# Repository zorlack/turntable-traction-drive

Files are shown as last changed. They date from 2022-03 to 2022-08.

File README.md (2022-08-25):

# Turntable Traction Drive Project

<image alt="Design Render" src="images/design-render.jpg" width=600 />

This is my design for a Turntable Traction Drive. It's meant to turn a large theatrical turntable covered in sets and actors in a safe reliable way. It can be built for less than $3000 USD.

I was inspired to take on this project by Alan Hendrickson's chain-driven design featured in [Technical Designs Solutions for Theatre Volume 2 (Sammler/Harvey 2002)](https://www.amazon.com/Technical-Design-Solutions-Theatre-Collection/dp/0240804929). His design shows how a chain drive can rotate a turntable. I was interested in designing an easier-to-integrate "bolt-on" solution.

Feel free to make your own or iterate on this in any way permitted by the [license](LICENSE)! If you do happen to build one, send me a picture, I'd love to share it!

This project [has a website.](https://zorlack.github.io/turntable-traction-drive/)

## Critical Documents

| Document Name | Description |
| -- | -- |
| [Safety and Liability](SAFETY.md) | Discussion of the drive and safety factors associated with its use. |
| [Design Document](DESIGN.md) | Discussion of design and considerations made. |
| [Parts Sourcing Guide](SOURCING.md) | Instructions on how to buy the right parts to build your own Turntable Traction Drive. |
| [Assembly Guide](ASSEMBLY.md) |  Instructions on how to build your own Turntable Traction Drive.  |
| [Integration Guide](INTEGRATION.md) | Instructions for Technical Directors on how to integrate this machine into your set desgin. |
| [Operation Guide](OPERATION.md) | Instructions for Technical Directors on how to operate this machine. |
| [Bill Of Materials](BOM.md) | A list of the parts required to build this machine. |
| [Wiring Guide](WIRING.md) | Instructions for wiring up the VFD, Control Pendant, and Emergency-Stop. |
| [Custom Parts Overview](TurntableTractionDrive-PartsOverview.pdf) | A one-page PDF helpful when ordering custom cut steel. |
| [Creative Commons Attribution 4.0 International](https://github.com/zorlack/turntable-traction-drive/blob/master/LICENSE) | The license under-which these plans are made available. |

## Checklists

| Document Name | Description |
| -- | -- |
| [Integration Checklist](INTEGRATION.md#integration-checklist) | A list of integration requirements for safe scenic integration of the Turntable Traction Drive. |
| [Operations Checklist](OPERATION.md#operations-checklist) | A "preshow" checklist to verify before each use of the Turntable Traction Drive. |

## Part Files

| Part | Description |
| -- | -- |
| [Chassis Parts](https://github.com/zorlack/turntable-traction-drive/tree/master/dxfs) | 2D CAD drawings of chassis parts to be cut from 1/4" mild steel. | 
| [Safety Placard](TurntableTractionDriveLabel.pdf) | A PDF to be made into a printable label and applied to the top of the chassis. | 

## Media

- [Assembled Chassis Before Welding (photo)](parts-fitup.jpg)
  
  <image alt="Assembled Chassis Before Welding (photo)" src="images/parts-fitup.jpg" width=400 />

- [Initial Bench Test (video)](https://youtu.be/k4kjQTp1Dig)
  
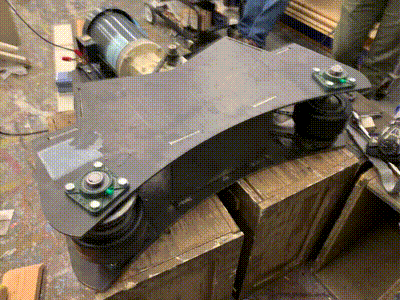
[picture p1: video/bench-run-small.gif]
Bench Test (https://youtu.be/k4kjQTp1Dig)
  

- [Startup Run (video)](https://youtu.be/NJ8Oi7qZh6Y)

  Startup Run (https://youtu.be/NJ8Oi7qZh6Y)

- [Full Speed Run of 23' Turntable (video)](https://youtu.be/Ed3DXH9XDa4)

  Full Speed Run of 23' Turntable (https://youtu.be/Ed3DXH9XDa4)
  
- [Full Speed Run of 6' Turntable (video)](https://youtu.be/193OzLW5t50)

  Full Speed Run of 6' Turntable (video) (https://youtu.be/193OzLW5t50)
  
- [Rehearsing on a 6' Turntable (video)](https://youtu.be/gqXYZ6G5New)

  Rehearsing on a 6' Turntable (video) (https://youtu.be/gqXYZ6G5New)

## Turntable Traction Drive Specifications

| Traction Drive Feature |  Detail |
| --- | ---|
| Design Units | **INCHES** |
| Height | 9.875" |
| Width | 32.875" |
| Depth |  33" |
| Chassis Weight | ~112 Lbs |
| Total Weight | ~228 Lbs |
| Number of Parts | 63 |
| Minimum Turntable Size | 6' Diameter |
| Maximum Turntable Size | Proven on a 23' diameter Turntable with steel and wood scenery. |

### Powerplant Details

My motor decision was based on what I had lying around. You may easily sub in your own motor, but for simplicity of integration try to pick a motor matching NEMA Frame 145TC. Otherwise you may have to drill new holes in the `Base Plate` and `Motor Gusset`.

| Powerplant Feature |  Detail |
| --- | ---|
| Model | General Electric 2HP TEFC (5KE48WN8167) |
| Speed | 1725 RPM at 60Hz |
| Layout | NEMA Frame 145TC |
| Gearhead | Morse 175Q140LR5 |
| Gearhead Ratio | 5:1 |

### Control Details

In order to vary the speed of drive motor we must use a Variable Frequency Drive (VFD). The VFD will be responsible for managing the speed and acceleration of the traction drive. 

#### VFD for 3 Phase Power (208 VAC)
In our environment we have easy and plentiful access to 3phase 208v. For this reason we have selected a 3phase input VFD. If you have access to 3 phase power you can benfit from our integration notes throughout this documentation.

| VFD Feature |  Detail |
| --- | ---|
| Model | Automation Direct DURA Pulse (GS23-22P0)  |
| Input Power | 230V 3-Phase (208 is fine) |
| Output Power | 1.5 KW (2 HP) |
| Output Range | 0 - 600Hz |
| Safe Torque Off (STO) | Yes |

#### VFD for Single Phase (120 VAC)
Our initial testing was performed on a .75 KW 120V VFD. We were able to easily turn the 23' turntable using just a single wall outlet.

| VFD Feature |  Detail |
| --- | ---|
| Model | Hitachi L-100 (L100-007NFU)  |
| Input Power | 120VAC 15A |
| Output Power | 0.75 KW (1 HP) |
| Output Range | 0 - 360Hz |
| Safe Torque Off (STO) | **No** |

We decided to replace this VFD for two reasons:

- In our environment 3-phase 208 is easily availble, and since 1HP isn't really up to the demands of our motor, the testing VFD didn't make a lot of sense.
- The intial wiring design of our e-stop buttons was not up to industrial automation standards. Critically, the e-stop was unable to constrain a runaway VFD. As a hedge agasint this risk we have selected a VFD with a Safe Torque Off (STO) feature. This feature adds independant hardware designed to reliably disconnect the output transistors of the VFD from the motor.

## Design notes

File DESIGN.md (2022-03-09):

# Turntable Traction Drive Design

Staples Players was looking for a way to add some automation and motion to its production of Disney's Descendants The Musical. I was interested in creating a solution which could be applied generically to any of the typical turntable configurations they use.

I decided to make a drive unit to rotate a turntable by applying a traction wheel against the edge of the table. Such a device would be easy to integrate in most sets where the turntable sits on top of the stage floor.

## Mechanical Considerations

Using drive wheels to turn a turntable seemed pretty straight forward. I'm pretty sure I've seen carnival rides driven in this manner. As a gut-check I did a bit of marketplace research and found that such devices do exist.

<image alt="Concept" src="images/initial-concept.png" width=600 />

My first idea was to use a motor with a gear reduction and a triangular chain configuration. The friction wheels would be pneumatic tires. The idea was that an idler would pull the chain away from the contact-point of the turntable and allow for easy tensioning of the chain system. However, preliminary research indicated two things: First, chains don't like to be run horizontally they prefer to run vertically. Second, a triangular configuation would result in an uneven distribution of power between the two drive wheels.

<image alt="Design Layout" src="images/design-layout.jpg" width=400 />

Moving away from the single-chain configuration I moved towards a centrally mounted motor with two chains, one going to each drive shaft. I also ditched the idea of pneumatic wheels and prefering instead an off-the-shelf keyed drive roller from McMaster. This simplified sourcing and answered the question: How do I attach the drive shaft to the wheel.

<image alt="Design Render" src="images/design-render.jpg" width=400 />

With those two decisions made the next step was to make a design in Fusion 360 and start selecting components. I started with the power source. I was eager to use a motor I had sitting on the shelf: A 3 Phase 2HP GE Motor (NEMA Frame 145TC. GE Model 5KE48WN8167) with a Morse 5:1 right-angle gear reduction (Morse 175Q140LR5.) This is a fairly beefy motor with a significant gear reduction.

| |  Motor Shaft | Gear Box Output | Output Wheel |
| -- | --- | -- | -- |
| Ratio | 1:1 (1.0) | 5:1 (.20) | 11:30 (.36) |
| RPM @ 60Hz | 1725 RPM | 345 RPM | 124 RPM |

In addition to the gear reduction on the front-end of the motor, I wanted to further reduce the gearing for two reasons: First, turntables typically require a large amount of effort to break free when turning. Reduced gearing would permit greater starting torque. Second, the native speed of the motor and gearing is 345 RPM (1725 RPM / 5). We want the traction drive gearing to allow us to use as much of the 0-60Hz range of the motor as possible without spinning a turntable too quickly. Therefore care was taken to use a small drive sprocket (11 teeth), a large axle-sprocket (30 teeth), and a small drive wheel (6" diameter".)

| Effective Speed Math | |  |
| -- | -- | -- |
| Drive Wheel Circumference (feet) | 2π * .25' | 1.57' Foot Circumference |
| Linear Feet Per Minute | 124 RPM * 1.57' | 194 Feet Per Minute |
| 6' Diameter Turntable Max Speed | 194 FPM ÷ 19' | 10.2 RPM (Measured: 11.3 RPM) |
| 16' Diameter Turntable Max Speed | 194 FPM ÷ 50' | 3.8 RPM |
| 23' Diameter Turntable Max Speed | 194 FPM ÷ 72' | 2.6 RPM (Measured: 2.7 RPM)|

**Integration Note:** *If you find that the drive speed is not large enough for your large turntable design, your best bet, depending on your choise of motor and VFD, is to overdrive the motor past 60Hz. (Most VFDs let you run up to 360Hz, but you will want to check your motor and drive documentation first.) Alternatively you could swap out the 6" drive wheels for a larger diameter wheel, but be aware that this will reduce the available startup torque.*

<image alt="Right Bearing Gusset" src="images/right-gusset.jpg" width=400 />

The Turntable Traction Drive is designed to sit on a flat surface. Because of this I couldn't through-bolt the pillow block bearings. That means that the steel would have to be drilled and tapped. Because the steel is only 1/4" I would need additional thickness on the bottom layer in order to have appropriate thread engagement. To resolve this, I designed three "gusset" parts: Two supporting the lower bearings and one supporting the motor mount. They are meant to be welded down then drilled and tapped, such that the threads are continuous.

## Turntable Eccentricity

Turntables aren't perfect circles, and they're not always perfectly centered, so I needed somehow to keep the machine pressed against the side of the turntable even if it's out-of-true. I designed the machine with four 200lb springs which could be set to provide significant preload against the side of the turntable. 

<image alt="Pusher Springs" src="images/pusher-plate.jpg" width=400 />

The springs are held captive by a 5/16" bolt welded to the pusher plate. The springs press against a piece of 1.5" angle iron which is lag-bolted through the two slots to the stage floor. This allows the whole machine to slide back and forth in response to bulges or dips in the circumference of the turntable.

<image alt="Ratchet Straps" src="images/ratchet-straps.jpg" width=400 />

When testing we found that a far simpler solution was to use ratchet straps to draw the machine up against the side of the turntable and hold it there. Ratchet straps have some natural elasticity and therefore provide similar preload to a spring-based solution with substantially easier integration. (We can turn a large turntable witout even bolting the machine to the deck!)

## Chain Tension

Chain based system must be kept in tension to keep the chain from slipping off the drive sprocket. In order to apply tension to the system we mounted the drive motor on top of [an adjustable sled from McMaster](https://www.mcmaster.com/62035K23/). However, we noticed too late that the sled is meant to adjust the position of a motor mounted perpendicularly to the track of the sled. My design called for the motor to be mounted parallel with the track.

<image alt="Motor Modifications" src="images/motor-mods.jpg" width=200 />

In order to mount the motor in this orientation we had to drill two additional holes in the motor's NEMA 146TC mounting plate. Once drilled we could use the drive seld to tension the chain and then crank down the motor bolts to lock it in place.

## Material

Because I didn't know how much force would be required to turn a loaded-turntable I wasn't able to do any real load calculations. Without this knowlege it seemed the best bet was to over-build the system. So I designed around plasma-cut 1/4" A36 mild steel. 

<a href="TurntableTractionDrive-PartsOverview.pdf"><image alt="Steel Order" src="images/design-sample.jpg" width=400 /></a>

I made a tab-and-slot design such that when assembled the machine would (hopefully) hold itself square long enough for me to weld it together. I allowed for 1/16th of clearance between my tabs and my slots and verified that the steel shop could hold 1/16 tolerance during plasma cutting. Their advice was that as long as no holes were smaller than 0.25" they should have no problems holding 1/16" tol.

<image alt="Steel Order" src="images/steel-qa.jpg" width=400 />

I provided the steel shop with a flat DXF file for each part with **INCHES** as the unit. They sent me back some fully dimensioned scans for me to verify.

<image alt="Parts Fitup" src="images/parts-fitup.jpg" width=400 />

Chapin and Bangs in Bridgeport, CT made the steel parts. They were made out of A36 steel, plasma cut, delivered dry. The cost was $810 with delivery.

<image alt="Initial Welds" src="images/initial-welds.jpg" width=400 />

The biggest problem with 1/4" steel is that my welder is only barely powerful enough to weld it. I ended up using .030 flux-core wire. Flux-core welds don't look great but they're plenty strong and I was able to get reasonable penetration even with my wimpy 120VAC welder.

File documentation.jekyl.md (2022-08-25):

---
permalink: /documentation
title: Turntable Traction Drive
description: Complete Documentation
---

<image alt="Design Render" src="images/design-render.jpg" width=600 />

This is my design for a Turntable Traction Drive. It's meant to turn a large theatrical turntable covered in sets and actors in a safe reliable way. It can be built for less than $3000 USD.

I was inspired to take on this project by Alan Hendrickson's chain-driven design featured in [Technical Designs Solutions for Theatre Volume 2 (Sammler/Harvey 2002)](https://www.amazon.com/Technical-Design-Solutions-Theatre-Collection/dp/0240804929). His design shows how a chain drive can rotate a turntable. I was interested in designing an easier-to-integrate "bolt-on" solution.

# Table of Contents

- [Safety](#safety-and-liability)
- [Design Document](#turntable-traction-drive-design)
- [Parts Sourcing Guide](#parts-sourcing-guide)
- [Assembly Guide](#turntable-traction-drive-assembly-guide)
- [Integration Guide](#turntable-traction-drive-integration-guide)
- [Operation Guide](#turntable-traction-drive-operation-guide)
- [Bill of Materials](#bill-of-materials)
- [Wiring Guide](#wiring-guide)
- [License](#license)

{% include_relative  SAFETY.md %}

{% include_relative  DESIGN.md %}

{% include_relative  SOURCING.md %}

{% include_relative  ASSEMBLY.md %}

{% include_relative  INTEGRATION.md %}

{% include_relative  OPERATION.md %}

{% include_relative  BOM.md %}

{% include_relative  WIRING.md %}

# License
```
{% include_relative LICENSE %}
```

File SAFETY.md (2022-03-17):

# Turntable Traction Drive Safety and Liability

As it's intended use involves live actors on a rotating stage, the safety of the Turntable Traction Drive must be considered seriously. But before we dig into a risk assesment understand this: 

**I am not an engineer.** I write software for a living and am not formally trained to assess safety risks. As such, **any risk assesment made here should not be considered comprehensive.**

In undertaking this project, and making it publicly available, it behooves me to draw attention to this fact, as well as to to state clearly that **I don't guarantee that this design works as intended, and I am not liable for any harm resulting from your use of this design.**

## Liability

This design is available for use under the [Creative Commons Attribution 4.0 International license](https://github.com/zorlack/turntable-traction-drive/blob/master/LICENSE). By using this design you agree to the terms of this license.

The license includes the following language, which you should read:

    Section 5 -- Disclaimer of Warranties and Limitation of Liability.

      a. UNLESS OTHERWISE SEPARATELY UNDERTAKEN BY THE LICENSOR, TO THE
         EXTENT POSSIBLE, THE LICENSOR OFFERS THE LICENSED MATERIAL AS-IS
         AND AS-AVAILABLE, AND MAKES NO REPRESENTATIONS OR WARRANTIES OF
         ANY KIND CONCERNING THE LICENSED MATERIAL, WHETHER EXPRESS,
         IMPLIED, STATUTORY, OR OTHER. THIS INCLUDES, WITHOUT LIMITATION,
         WARRANTIES OF TITLE, MERCHANTABILITY, FITNESS FOR A PARTICULAR
         PURPOSE, NON-INFRINGEMENT, ABSENCE OF LATENT OR OTHER DEFECTS,
         ACCURACY, OR THE PRESENCE OR ABSENCE OF ERRORS, WHETHER OR NOT
         KNOWN OR DISCOVERABLE. WHERE DISCLAIMERS OF WARRANTIES ARE NOT
         ALLOWED IN FULL OR IN PART, THIS DISCLAIMER MAY NOT APPLY TO YOU.

      b. TO THE EXTENT POSSIBLE, IN NO EVENT WILL THE LICENSOR BE LIABLE
         TO YOU ON ANY LEGAL THEORY (INCLUDING, WITHOUT LIMITATION,
         NEGLIGENCE) OR OTHERWISE FOR ANY DIRECT, SPECIAL, INDIRECT,
         INCIDENTAL, CONSEQUENTIAL, PUNITIVE, EXEMPLARY, OR OTHER LOSSES,
         COSTS, EXPENSES, OR DAMAGES ARISING OUT OF THIS PUBLIC LICENSE OR
         USE OF THE LICENSED MATERIAL, EVEN IF THE LICENSOR HAS BEEN
         ADVISED OF THE POSSIBILITY OF SUCH LOSSES, COSTS, EXPENSES, OR
         DAMAGES. WHERE A LIMITATION OF LIABILITY IS NOT ALLOWED IN FULL OR
         IN PART, THIS LIMITATION MAY NOT APPLY TO YOU.

In plain language: **I don't guarantee that this design works as intended, and I am not liable for any harm resulting from your use of this design.**

## Limitations

The Turntable Traction Drive has the following known limitations/deficiencies:

- No Brake: The Turntable Traction Drive does not provide built-in braking. (This may be remedied by using a motor configuration with a power-off brake.) In practice this means that when the drive is not rotating the turntable is only kept in place by two things: The inertia of the turntable itself, and the friction in the chain and gearbox system of the Turntable Traction Drive. For massive (high-mass) turntables with substantial loss due to friction this is not a problem, as the turntable will tend to stay put. **For low-mass or low-friction turntables it may be neccessary to use an external braking mechanism to keep the turntable from free-rotation when the drive is not rotating.**
- Insufficient Current Limiting Capabilities: Ideally we would like to set a current limit at various stages of operation such that the inverter trips when there is an unexpected spike in current. **The Hitachi L100-007NFU does not have sufficiently granular current-limit controls.**
- Open Loop: The Turntable Traction Drive is a machine for rotating a turntable. It is not a machine for accurately "positioning" a turntable. As such **this machine's utility in precise motion control applications may be limited.**

## Key Safety Principals

:warning: **The Turntable Traction Drive is a powerful machine. Using it should not be taken lightly. Caution and care must be taken in every integration to ensure that safe operating parameters are configured.**

A turntable may pose a hazard on set even when operated manually by backstage technicians, however, unlike backstage technicians this machine has no brain. It doesn't know to stop because a piece of scenery is late during a scene-shift. It is not context-aware. Also, unlike a backstage technician, under the right circumstances this machine can summon inhuman amounts of torque.

:warning: **Due to its power and remoteness this machine is not designed as part of an automation system. Rather, it is intended to be manually operated by a user with a clear view of the turntable.**

The Turntable Traction Drive has exposed moving parts and therefore poses some first-hand risk of injury to operators. However, when attached to a turntable new hazards may appear.

:warning: **A scenic turntable creates risks of injury independant of the drive mechanism. Take care to evaluate the risks not just from the Turntable Traction Drive, but from the system as a whole.**

## Risk Management

As some risk is unavoidable, my analysis will focus on mitigation strategies. Any requirement layed out in this section must be specifically required in either the Integration Checklist or Operations Checklist.

| Risk | Mitigation Strategy |
| -- | -- |
| Risk of electrical shock | **Requirements:**<br/>Ground VFD appropriately to input mains.<br/>Ground motor appropriately to VFD.<br/>Ground chassis appropriately to the motor chassis. |
| Pinching hazards from exposed rotating machine parts. |  **Requirement:**<br/>Turntable Traction Drive must be in a fully enclosed secure area during operation. |
| Pinching/Crushing hazards between traction wheels and turntable edge. | **Requirement:**<br/>Interface between the turntable and the traction drive must be fully enclosed during operation. |
| Risk of unexpected start | **Requirement:**<br/>Enable Unattended Start Protection in VFD by setting `c04` to `13` and short `P24` to `PIN 4`<br/>Disconnect power from the system prior to maintenance. |
| Risk of fall during normal operation | **Requirements:**<br/>Rehearse with onstage personel in order to find safe speeds and acceleration values. Do not deviate from these values without notice. |
| Risk of fall due to sudden acceleration | **Requirement:**<br/>Use conservative acceleration/deceleration values when configuring VFD. (For Hitachi L-100 see settings `f01`, `f02`, and `f03`) |
| Risk of fall due to overspeed | **Requirement:**<br/>Set a conservative hard frequency limit in your VFD configuration. (For Hitachi L-100 see settting `a61`) |
| Risk of crushing | **Requirement**<br/>Where possible tune-narrowly the current limiting features of your VFD. (For the Hitachi L-100 this configuration may be limited.) |
| Risk of crushing because of external scenery-based crush points. | **Requirements:**<br/>Turntables must maintain a raidal safety margin sufficient to prevent a person from being caught between a rotating piece of scenery and any adjacent piece of scenery.<br/>Emergency Stop button must located near the turntable.<br/>Cast and crew must be trained on the location of the Emergency Stop button. |
| Risk of entanglement | **Requirements:**<br/>Operator must have a clear view of the turntable.<br/>Emergency Stop button must located near the turntable.<br/>Cast and crew must be trained on the location of the Emergency Stop button. |
| Risk of slipping on a free-rotating turntable | **Requirement**<br/>A parking brake (or other disablement device) must be employed to prevent the turntable from turning when the Turntable Traction Drive is not in use.<br/>All on-stage personel must be instructed on the free-rotating-nature of the turntable. |
| Risk of operator/integrator ignorance | **Requirements:**<br/>All safety requirements and warnings must be clearly printed on a label applied to the machine.<br/>Documentation must be made available. |
| Risk of structural collapse on turntable | **Requirement:**<br/>Ensure that all scenery is constructed such that it can absorb tortional load such as might result from a sudden change in rotational speed. |

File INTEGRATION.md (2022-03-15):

# Turntable Traction Drive Integration Guide

This guide is designed to help scenic designers and technical directors integrate the Turntable Traction Drive into their sets.

:warning: **Before Proceeding, make sure you have read and understood the [SAFETY](SAFETY.md) section of the documentation.**

:warning: **Before Proceeding, make sure you have read and understood the [Limitations](SAFETY.md#Limitations) section of the documentation.**

## Turntable Integration

The Turntable Traction Drive applies significant forces to the side of the turntable where it makes contact. This requires the following considerations:

- The Turntable Traction Drive should not be pressed against a surface which will bow or deflect under pressure. Ideally you'd want a 3" wide rigid band that the turntable can drive against. In practice we've found that the drive wheels can get plenty of traction when applied against the edge of a 1.5" laminated plywood floor.
- The drive wheels of the traction drive may cause maring or discoloration of surface finishes. You may need to apply a protective coating to traction surfaces if they are visible to the audience.
- The drive wheels of the traction drive apply force to just one side of a turntable. To keep the turntable centered on its rollers your centering device must be sufficiently rigid (and well lubricated) to counter this force. 

### Critical Dimensions

The two key factors when determining if this machine will work with your turntable are diameter and mass. At present we don't have sufficient information to give guidance about maximum turntable mass. Except to say that we had no difficulty moving a 23' turntable with a 2-story wood and steel "castle" on it.

| Dimension | Value |
| -- | -- |
| Minimum Turntable Diameter | 6' |
| Maximum Turntable Diameter | 23' Demonstrated (Maximum Unknown) |

If the diameter of your turntable is too large you may have difficulty running it fast enough with the as-designed gearing. If this is the case you have two options:

- You may increase the diameter of your drive rollers up to 12" in diameter (this size is quite extreme consider 8"). Increasing the diameter of the drive rollers will cause you to suffer a substantial loss of starting torque. The advantage is increased speed at your motor's native frequency without an increase in chain noise. 
- You may decide to overdrive your motor beyond 60Hz. Many VFDs will let you run the motor up to 400Hz, at this speed you would likely damage your gearbox, motor and chain drive. Many motors will be perfectly happy to run faster than 60Hz with reduced duty cycle. Consult your motor and gearbox documentation to determine the maximum safe operating speed of your Turntable Traction Drive.

Another critical factor is the height of the traction-bearing surface relative the bottom of the turntable traction drive. The vertical position of the drive wheels is adjustable, but is ultimately constrined by the spacing between the drive sprockets. That said drive wheels have about 4" of vertical adjustability.

| Dimension | Value |
| -- | -- |
| Minimum Traction Surface Width | 1.5" |
| Maximum Traction Surface Width | 3" (Drive Roller Width) |
| Lowest Possible Traction Surface | 3.25" to 4.75" from the bottom of the machine |
| Highest Possible Traction Surface | 5.75" to 7.25" from the bottom of the machine |

If the traction surface of your turntable is too high, it may be neccesary to raise the machine so that it contacts the correct portion of the turntable. Conversely, it may be neccesary to mount your traction drive below the stage if your dive surface is too low.

## Traction Pressure

The available tractive force of the Turntable Traction Drive is related to the pressure applied by the rollers against the traction surface. In other words, it's not sufficient to place the Turntable Traction Drive next to a turntable, it must be pressed firmly against the side of it. 

This "preload" pressure may be created via two integration schemes:

### Ratchet Straps

In testing the Turntable Traction Drive we observed that we could apply ample force between the drive wheels and the turntable simply by connecting ratchet straps between the machine chassis and the carrier wheels of the turntable.

This system has several advantages over the Pusher Spring system:

- Rachet straps are plentiful and easy to inspect.
- The have some natural stretch to them, allowing for eccentricity of the turntable.
- They are easy to remove and reattach, simplifying maintenance activities.
- Rachet straps don't create metal-on-metal noise as they stretch.

For these reasons ratchet straps are prefered mecahnism for integration.

To attach the turntable via rachet straps:

- Ensure that the Turntable Traction Drive is evenly supported and that you have strong material under the lag-bolt slots.
- Connect the left and right sides between the rear of the side-panels and a suitably strong tie-down point on or near your turntable.
- Evenly tension the two belts such that drive wheels are in good contact with the turntable.
- Lag-bolt the machine down to the supporting surface loosely. (Such that the machine may become detached from the turntable, but may not be flung away from it.)

### Pusher Springs

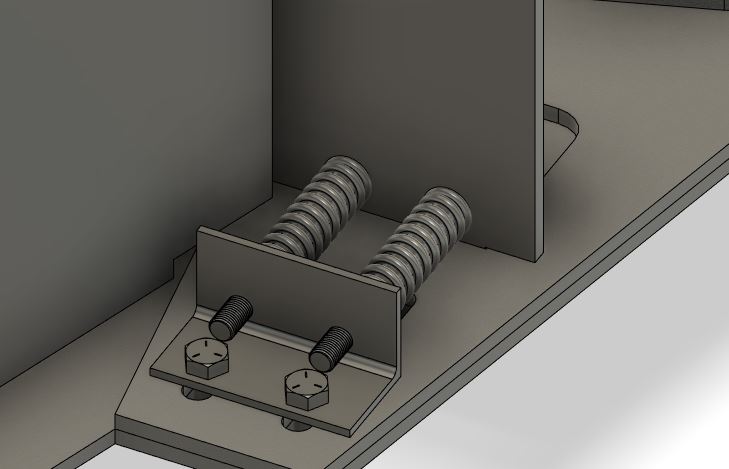
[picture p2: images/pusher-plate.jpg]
Pusher Springs


The design calls for the use of four pusher springs which ride on 5/16" guide bolts. These pusher springs push the turntable forward, away from two L-iron brackets anchored firmly to the deck. This mechanism allows for approximately 1.8" of eccentricity in the turntable circumference while applying around 200 lbs of force.

To install the pusher springs follow these instructions:

- Ensure that the Turntable Traction Drive is evenly supported and that you have strong material under the lag-bolt slots.
- Weld hex-heads the 5/16" partially-threaded guide bolts into the four holes provided in the pusher plates. The bolts should face backwards with the bolt heads resting on the interior faces of the pusher plates.
- Slide the pusher springs over the guide bolts.
- Pass the guide bolts into holes drilled in the L-iron. 
- Using 5/16" lock nuts, compress the pusher springs between the L-Iron and the pusher plates.
- Using lag-bolts, bolt the L-iron to the supporting surface. Make sure the lag-bolts pass through the slots on the bottom plate.
- Loosen the 5/16" lock nuts such that the springs expand between staticaly mounted L-iron and the movable Turntable Traction Drive.

*Note: In the pusher spring rendering there is insufficent clearance between the guide-bolts and the lag-bolts. This has been remedied by raising the holes in the pusher plate.*

## Integration Checklist

To help ensure safe operation of this Turntable Traction Drive please ensure the following **REQUIRED** conditions have been met:

| Requirement | Complete |
| -- | -- |
| Technical Director/Integrator must read and understand the [safety](SAFETY.md) section of this documentation. | :black_square_button: |
| Turntable Traction Drive chassis grounded to motor frame | :black_square_button: |
| Motor frame grounded to VFD | :black_square_button: |
| Turntable Traction Drive is fully enclosed in a secure area | :black_square_button: |
| Drive-wheel interface points are fully enclosed | :black_square_button: |
| Turntable hard-scenery elements don't create opportunities for shearing or crushing | :black_square_button: |
| Emergency stop button located within 6' of Turntable Traction Drive | :black_square_button: |
| Turntable fitted with an external parking brake (or other disablement device.) | :black_square_button: |

## VFD Configuration

### DURApulse GS23-22P0 Configuration

**Note:** These notes are only really useful for the DURApulse GS23. If you're using another VFD consult your documentation.

When configured correctly we desire the following outcome:

- To tell the turntable to run forward short `DCM` to `DI1/FWD`.
- To tell the turntable to run in revers short `DCM` to `DI2/REV`.
- To enter Safe Torque Off `STO` interrupt short between `+24 V` and either `STO1` or `STO2`

#### DURApulse GS23 Parameters

| Parameter | Value | Notes |
| -- | -- | -- |
| `P02.00` | `2` | 2-Wire Configuration |
| `P01.10` | `60` | Output Frequency Upper Limit |
| `P01.12` | `1` | Acceleration Time 1 |
| `P01.13` | `1` | Deceleration Time 1 |
| `P06.12` | ?? | Current Limit 0-250% |

### Hitachi L100 Configuration

**Note:** These notes are only really useful for the Hitachi L-100. If you're using another VFD consult your documentation.

`P24` provides a 24V field reference voltage for use when powering the Control Terminals.

When configured correctly we desire the following outcome:

- To tell the turntable to run forward short `P24` to `PIN 1`.
- To tell the turntable to run in revers short `P24` to `PIN 2`.

#### Hitachi L100 Parameters

| Parameter | Value | Notes |
| -- | -- | -- |
| `a01` | `00` | `00`=Keypad/Potentiometer, `01`=Control Terminals, `02`=F01 Settings |
| `a02` | `02` | `01`=Control Terminals, `02`=Keypad Run Key |
| `a02` | `02` | `01`=Control Terminals, `02`=Keypad Run Key |
| `a61` | `60` | Set a hard limit on the output frequency of the VFD to never overdrive the motor. |
| `a04` | `60` | Set the "Base" Frequency. (The frequency at which the VFD emits full voltage) |
| `a05` | `60` | Set the "Max" Frequency (The frequency allowed during manual opeation) |
| `a97` | `00` | Set the Acceleration Curve: `00`=Linear, `01`=S-Curve |
| `a97` | `00` | Set the Deceleration Curve: `00`=Linear, `01`=S-Curve |
| `c01` | `00` | Configure Terminal 1: `00`=Run Forward
| `c02` | `01` | Configure Terminal 2: `01`=Run Reverse
| `f01` | `nn` | **Set the target frequency** |
| `f02` | `nn` | **Set the acceleration time** (The number of seconds it should take to get spin-up from 0Hz to `f01`Hz) |
| `f03` | `nn` | **Set the deceleration time** (The number of seconds it should take to get spin-down from `f01`Hz to 0Hz) |

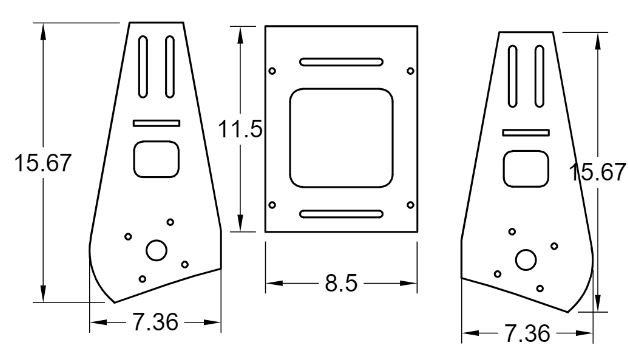
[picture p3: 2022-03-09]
images/design-sample.jpg

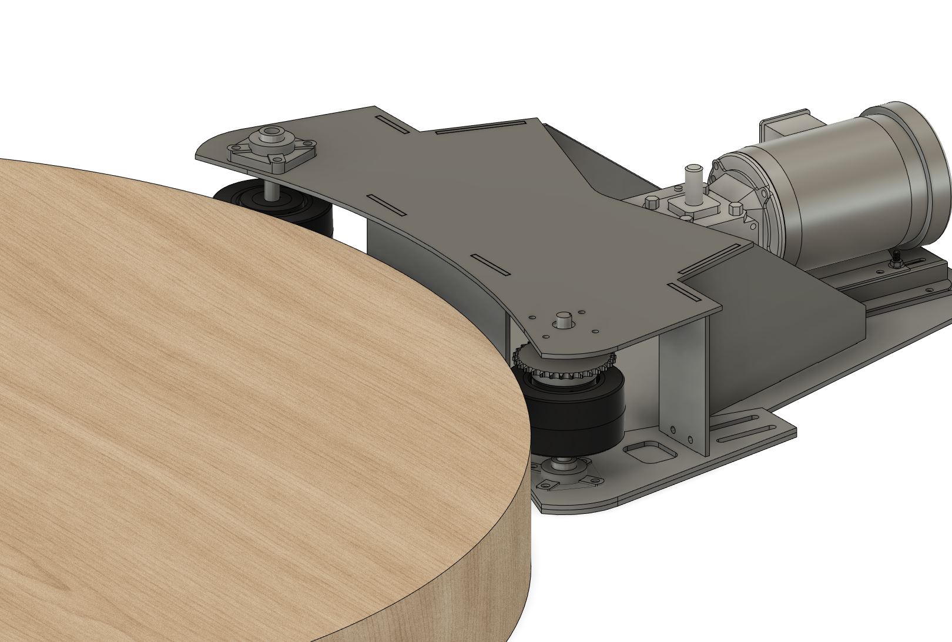
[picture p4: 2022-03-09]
images/design-render.jpg

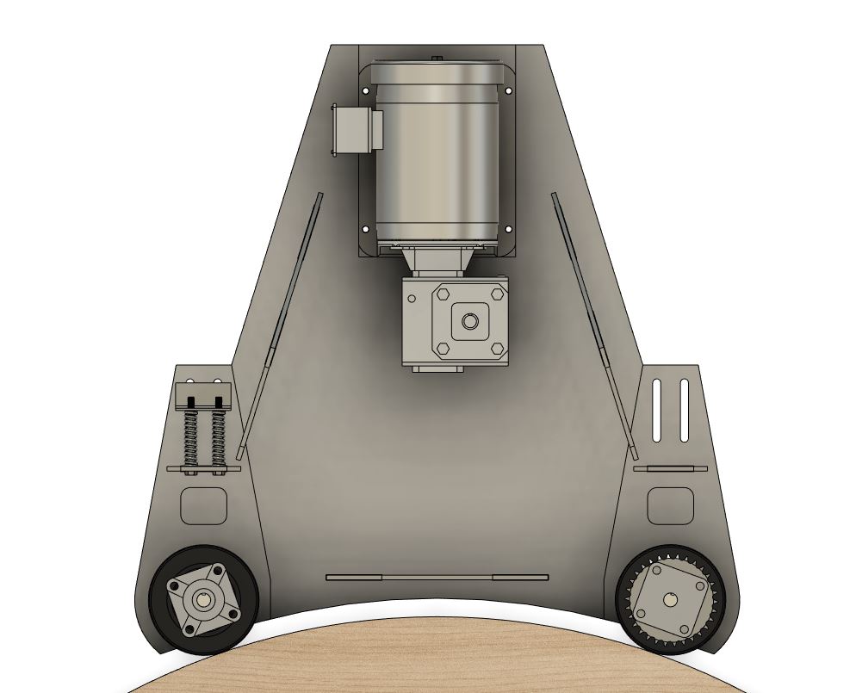
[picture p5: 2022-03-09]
images/design-layout.jpg

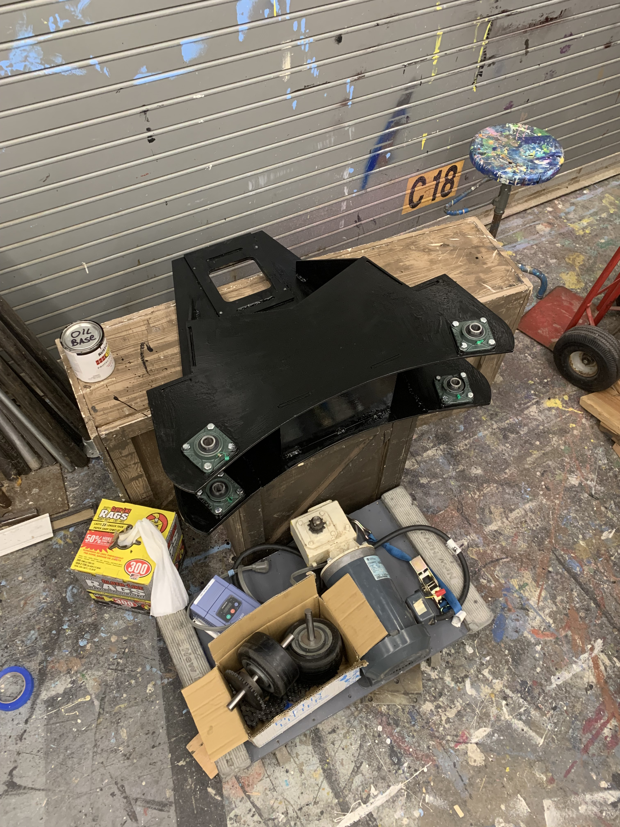
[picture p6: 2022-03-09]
images/painted-chassis.jpg

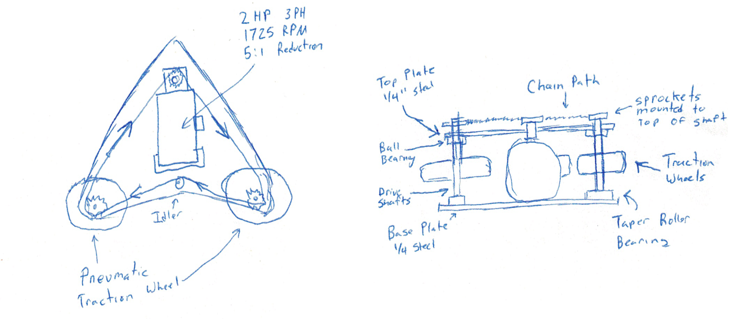
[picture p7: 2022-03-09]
images/initial-concept.png

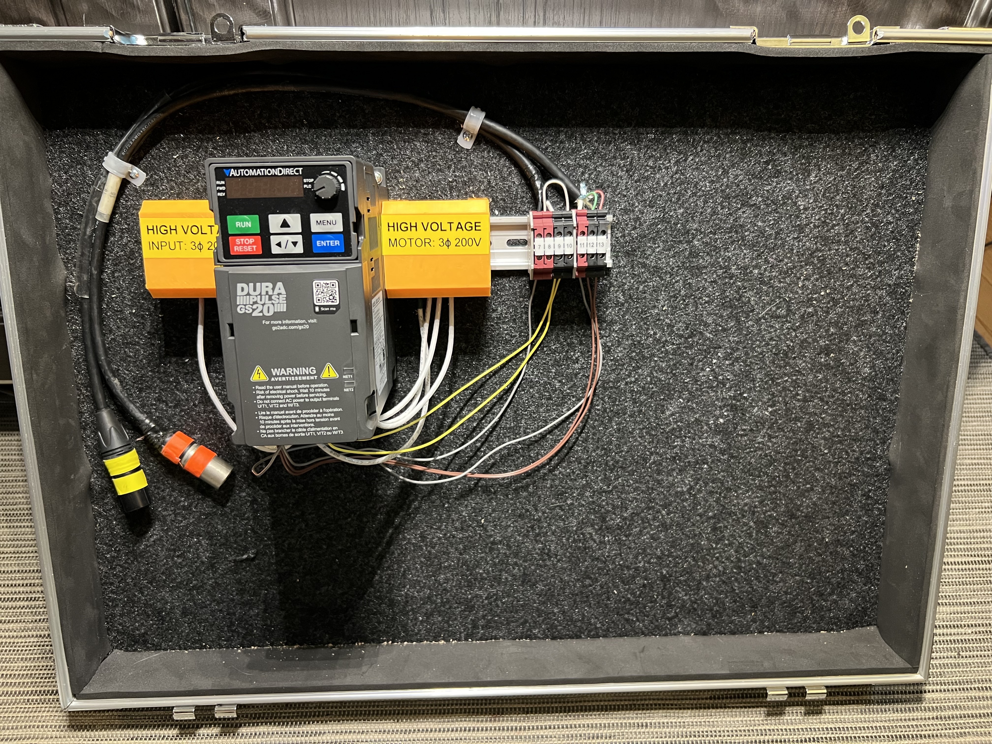
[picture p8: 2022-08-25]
images/control-panel.jpg

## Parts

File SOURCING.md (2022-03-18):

# Parts Sourcing Guide

Finding reliable sources for parts is a challenging problem. If you pick a vendor like Amazon you may find that your item SKUs are no longer available weeks after you've made a purchase. On the other hand if you source parts exclusively from McMaster-Carr and Grainger you'll be paying top-dollar for that consistency.

In order to make parts-sourcing consistant I've chosen McMaster-Carr for most pieces of hardware. The Motor, Gearbox, VFD and Custom Steel you will need to source independently.

## Bill Of Material

This project has a [Bill of Material](BOM.md). The BOM is a list of all the parts we used construct this machine. Wherever possible I have added links which (hopefully) will not go stale quickly. In addition I've added price estimates, but you should expect these numbers to change with time.

I reccomend that you source the hard parts first before placing a large order with McMaster-Carr. Make sure you can find all the relevant components at a price-point which meets your budget before you click "Check Out."

## Sourcing The Motor

The motor, and gearbox can be the most difficult parts to source. If you try to match precisely what I have used you will end up paying top-dollar. A more economical way to source the powertrain is to go on ebay and look for a used parts. Here are the important parameters:

| Feature | Value |
| -- | -- |
| NEMA Frame | 145TC |
| RPM | 1725 |
| Voltage | 208-230 |
| Phases | 3 |

The frame designation describes the precise size and layout of the motor bolts and face. Motor RPM is listed because a 1725 (or 1800RPM) motor is better suited for high-torque applications. Voltage isn't really your problem (since the VFD will be creating the motor voltage) all you really want to do is make sure you're selected a 200V class motor. Three phase is specified because this is necesary for the inverter to control the speed of the motor.

If you deviate too much from this prescription you may have to customize the `Base Plate` and `Motor Gusset` parts in order to fit your motor. You will also have to make sure your gear-reduction fits correctly.

## Sourcing The Gearbox

The gearbox we're using, a Morse 175Q140LR5, has a couple of important features:

| Feature | Value |
| -- | -- |
| Drive Ratio | 5:1 |
| Frame | 143/145TC |
| Shaft Output | Left + Right |
| Output Shaft Diameter | 7/8" |

This may be the hardest part to source cheaply. Ebay may be your best bet. You can be a bit flexible regarding the drive ratio and the output shaft diameter (if you vary the output shaft diameter you will have to choosed different sprockets from the BOM.)

## Sourcing The Variable Frequency Drive (VFD)

The Variable Frequency Drive (also commonly called an inverter) is an esential component of this system. It provides speed control and safety features neceesary to safely operate the Turntable Traction Drive.

For our implementation we have selected AutomationDirect's DURApulse GS23-22P0 VFD. We used the following selection criteria:

| Feature | Value | Note | Required |
| -- | -- | -- | -- |
| Number of Input Phases | 3&nbsp;(or&nbsp;1) | **This matches the supply we have access to.**<br/>We have easy-access to three-phase power, so this is a good choice for our environment. | YES |
| Nominal Input Voltage | 230&nbsp;VAC | **This matches the supply we have access to.**<br/>We have 3-phase 208VAC so this is the correct model. | YES |
| Horsepower By Phase | 2&nbsp;(or&nbsp;1) | **This matches the motor we have selected.**<br/>We have selected a 2HP motor, so we want a VFD rated for 2HP. The parentheses indicates that this VFD can power a 1HP motor when configured for single-phase 200VAC service. | YES |
| Safe Torque Off (STO) | YES | **This is safety requirement used by our e-stop system.**<br/>Having an STO feature means that our e-stop wiring will protect us even from a malfunction of the VFD itself. | YES |
| Current Limit Capability | 10%-250% | **This is a safety requirement.**<br/>This feature allows us to tune the max current available to the motor. This can help stall the system if there's an unexpected jam. | YES |
| UL/CE Listed | YES | Someone has looked at this device to make sure it meets minimum requirements for electrical safety. | NO |
| Freely available software. | YES | Having good software makes integration easier and can improve safety. | NO |
| Software Interface | USB | For PC-based configuration, USB is slightly easier to interface with than RS485. Even USB-B. | NO |
| Cost | $208 | That's a great price for the feature-set we're looking for. | NO |
| SEO | Excellent | Let's be honest, the reason I zeroed in on this VFD is that Automation Direct has good online advertising and search engine optimization. | NO |

### 120VAC Power Single Phase

We have successfully powered our traction drive using a single 20A 120VAC mains circuit connected to a Hitachi L-100 VFD. If you only have access to single-phase 120VAC power you should seek a VFD which matches this configuration. Be aware that you will never be able to run a 2HP motor at maximum power using a 1HP VFD. You will likely also want to reduce your duty cycle in this configuration and should expect to produce extra heat. **That said, we had no difficulty in rotating our 23' turntable on a single 120VAC 20A circuit.**

Also be aware that VFDs under load have a nasty habbit of tripping residential breakers (especially RCD/GFCI circuits.)

## Sourcing the Custom Steel Parts

I found that it was a relatively simple matter to provide a local steel shop with the [2D DXFs](dxfs/) and the [Custom Parts Overview](TurntableTractionDrive-PartsOverview.pdf). The PDF makes it easy for a sales guy to quote the job without needing CAD. The PDF also communicates expectations around minimum hole diameter and tolerances.

The design allows for 1/16 of slop between slots and tabs. The steel fabiractor must be able to hold 1/16th tolerance. The steel company which we worked with said that their plasma process could hold 1/16" of tollerance, but they had a specific requirement that no holes be smaller than 1/4" in diameter. This is not a problem for this design as we have so indicated in the [Custom Parts Overview](TurntableTractionDrive-PartsOverview.pdf).

The total weight of the custom parts is around 112 lbs. Make sure you have a spot where the steel shop can deliver the order easily. In our experience the parts are, individually, easy to move around. When bundled together as a single order the steel is a two-person lift.

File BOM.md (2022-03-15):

## Bill Of Materials

| Component | Units | Quantity | Unit Cost | Notes |
| -- | -- | -- | -- | -- |
| **Control** | | | | |
| Automation Direct DURApulse GS23-22P0* | EA | 1 | $208 | [Variable Frequency Drive](https://www.automationdirect.com/adc/shopping/catalog/drives_-a-_soft_starters/ac_variable_frequency_drives_(vfd)/general_purpose/gs23-22p0) |
| Automation Direct GS20A-DR-AB | EA | 1 | $5 | [VFD 35mm DIN rail adapter.](https://www.automationdirect.com/adc/shopping/catalog/drives_-a-_soft_starters/ac_variable_frequency_drives_(vfd)/remote_keypads,_disconnects,_mounting_-a-_accessories/gs20a-dr-ab) |
| VFD Power Cable | EA | 1 | | #10 3-Wire Appliance Cable |
| VFD Power Connector | EA | 1 | | NEMA 5-15P |
| Control Pendant | EA | 1 | $36 | [Compact Crane Control Pendant](https://www.amazon.com/dp/B077NG3SLZ) |
| Emergency Stop Buttons | PACK | 1 | $14 | Mushroom Cap E-Stop Buttons |
| **Chassis** | | | | |
| Bottom Plate | EA | 1 | -- | Custom 1/4" Steel from [BottomPlate-TotalSketch.dxf](dxfs/BottomPlate-TotalSketch.dxf) |
| Motor Gusset | EA | 1 | -- | Custom 1/4" Steel from [MotorGusset-TotalSketch.dxf](dxfs/MotorGusset-TotalSketch.dxf) |
| Right Caster Gusset | EA | 1 | -- | Custom 1/4" Steel from [RightCasterGusset-TotalSketch.dxf](dxfs/RightCasterGusset-TotalSketch.dxf) |
| Right Pusher Plate | EA | 1 | -- | Custom 1/4" Steel from [RightPusherPlate-TotalSketch.dxf](dxfs/RightPusherPlate-TotalSketch.dxf) |
| Right Side Panel | EA | 1 | -- | Custom 1/4" Steel from [RightSidePanel-TotalSketch.dxf](dxfs/RightSidePanel-TotalSketch.dxf) |
| Left Caster Gusset | EA | 1 | -- | Custom 1/4" Steel from [LeftCasterGusset-TotalSketch.dxf](dxfs/LeftCasterGusset-TotalSketch.dxf) |
| Left Pusher Plate | EA | 1 | -- | Custom 1/4" Steel from [LeftPusherPlate-TotalSketch.dxf](dxfs/LeftPusherPlate-TotalSketch.dxf) |
| Left Side Panel | EA | 1 | -- | Custom 1/4" Steel from [LeftSidePanel-TotalSketch.dxf](dxfs/LeftSidePanel-TotalSketch.dxf) |
| Front Plate | EA | 1 | -- | Custom 1/4" Steel from [FrontPlate-TotalSketch.dxf](dxfs/FrontPlate-TotalSketch.dxf) |
| Top Plate | EA | 1 | -- | Custom 1/4" Steel from [TopPlate-TotalSketch.dxf](dxfs/TopPlate-TotalSketch.dxf) |
| Material, Plasma Cutting, Delivery | JOB | 1 | $811 | Custom Steel Cuttting to 1/16 Tolerance |
| Safety Label | JOB | 1 | -- | Custom Printed Vinyl Sticker from [TurntableTractionDriveLabel.pdf](TurntableTractionDriveLabel.pdf)  |
| **Input Side** | | | | |
| 3 Phase Electric Motor | EA | 1 | $600** | General Electric 2HP TEFC 5KE48WN8167 |
| Reduction Worm Gear | EA | 1 | $700*** | Morse 175Q140LR5 5:1 |
| Adjustable Motor-Mounting Base | EA | 1 | $40 | [62035K23](https://www.mcmaster.com/62035K23) Fits NEMA 145 and NEMA 145T Frames|
| Roller Chain Sprocket 11 Teeth | EA | 2 | $17 | [6280K654](https://www.mcmaster.com/6280K654) ANSI 40 Chain, 11 Teeth, for 7/8" Shaft Diameter |
| Motor Hold-Down Bolts | PACK | 1 | $7 | [92865A211](https://www.mcmaster.com/92865A211) Medium-Strength Grade 5 Bolt, 3/8"-24 Thread, 1/2" Long |
| Motor Cable | EA | 1 | | #10 4-Wire Appliance Cable |
| **Output Side** | | | | |
| Pillow Block Bearing  | PACK | 1 | $5 | [PGN - UCF204-12](https://www.amazon.com/dp/B07QQJP8SV), Pack of 4 |
| Keyed Rotary Shaft | EA | 2 | $21 | [1497K116](https://www.mcmaster.com/1497K116) - Fully Keyed, 3/4" Diameter, 9" Long |
| Keyed Drive Roller | EA | 2 | $118 | [61065K46](https://www.mcmaster.com/61065K46) - 6" Roller Diameter, 3" Roller Width, for 3/4" Shaft Diameter |
| Roller Chain Sprocket 30 Teeth | EA | 2 | $68 | [6236K331](https://www.mcmaster.com/6236K331) - ANSI 40 Chain, 30 Teeth, for 3/4" Shaft Diameter |
| Bearing Hold-Down Bolts | PACK | 1 | $15 | [92865A214](https://www.mcmaster.com/92865A214) Medium-Strength Grade 5 Bolt, 3/8"-24 Thread, 7/8" Long |
| **Spring Pusher** | | | | |
| 3" Pusher Spring | PACK | 1 | $13 | [9657K438](https://www.mcmaster.com/9657K438) Compression Spring, 3" Long, 0.75" OD, 0.48" ID, Pack of 6 |
| Partially Threaded Spring Guide Bolts | PACK | 1 | $15 | [91247A126](https://www.mcmaster.com/91247A126) Medium-Strength Grade 5 Bolt, 5/16"-24 Thread, 3-1/2" Long |
| Spring Guide Loading Nuts | PACK | 1 | $8 | [91247A128](https://www.mcmaster.com/91247A128) Medium-Strength Grade 5 Nut, 5/16"-24 Thread |
| **Miscelaneous** | | | | |
| Short Machine Key Steel | PACK | 1 | $3 | [98870A140](https://www.mcmaster.com/98870A140) - 3/16" x 3/16", 1" Long, Undersized, Pack of 10 |
| Long Machine Key Steel | PACK | 1 | $9 | [98870A192](https://www.mcmaster.com/98870A192) - 3/16" x 3/16", 3" Long, Undersized, Pack of 10 |
| #40 Roller Chain and Tools | PACK | 1 | $36 | [13 Pieces Roller Chain Disassembly Kit](https://www.amazon.com/dp/B094VL4JDD) |
| 3/8-24 Drill and Tap Kit | EA | 2 | $10 | [Drill America - POU3/8-24 3/8"-24](https://www.amazon.com/dp/B071XX6K6Z) |

**Total Cost Estimate: $2,980**

\* Choose a VFD that's compatible with your input power availability and which has a Safe Torque Off (STO) feature.

\*\* Price Estimate. There are lots of different motors [you can buy](https://www.grainger.com/product/U-S-MOTORS-General-Purpose-Motor-Totally-23J893). The most important thing is that the power and form-factor be correct. 

\*\*\* Price Estimate. There are lots of different gear reductions [you can buy](https://www.mscdirect.com/product/details/08433724). Make sure you pick one that will fit the motor you're using when rotated 90 degrees.

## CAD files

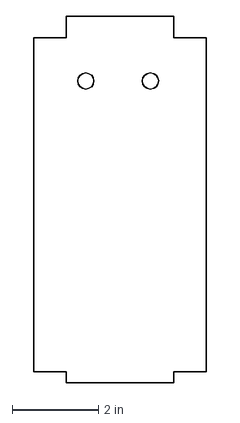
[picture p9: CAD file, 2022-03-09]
dxfs/RightPusherPlate-TotalSketch.dxf
4.00 x 8.50 in

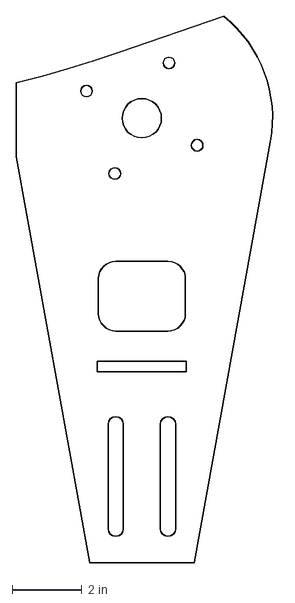
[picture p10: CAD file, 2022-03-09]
dxfs/LeftCasterGusset-TotalSketch.dxf
7.55 x 15.7 in

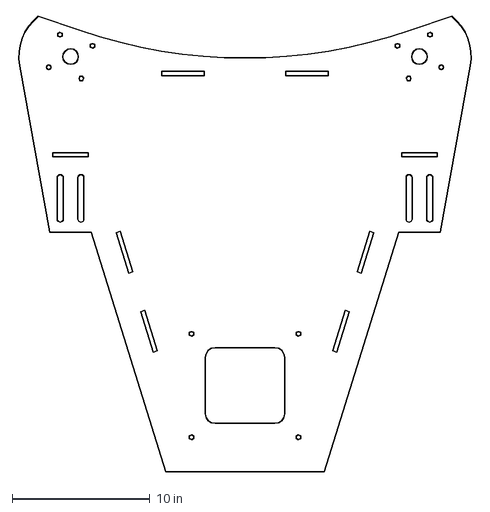
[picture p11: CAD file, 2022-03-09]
dxfs/BottomPlate-TotalSketch.dxf
33.2 x 33.0 in

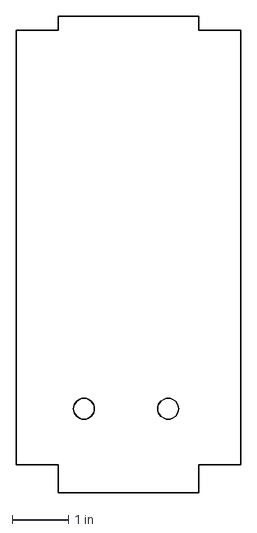
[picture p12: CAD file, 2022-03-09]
dxfs/LeftPusherPlate-TotalSketch.dxf
4.00 x 8.50 in

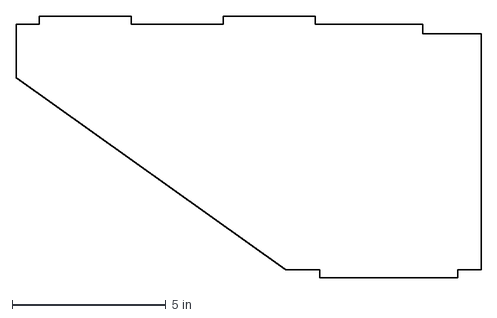
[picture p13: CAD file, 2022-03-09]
dxfs/RightSidePanel-TotalSketch.dxf
15.1 x 8.50 in

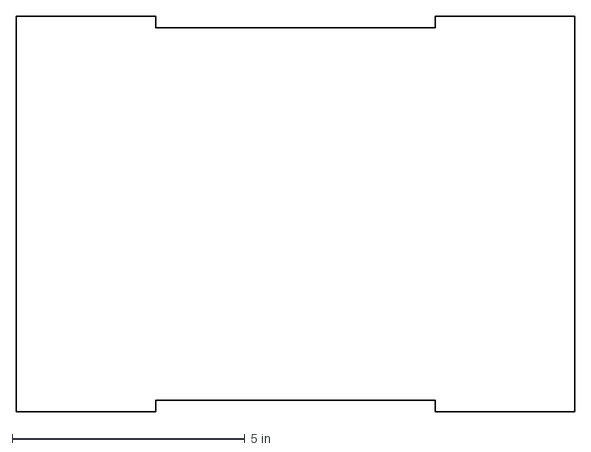
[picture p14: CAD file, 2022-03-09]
dxfs/FrontPlate-TotalSketch.dxf
12.0 x 8.50 in

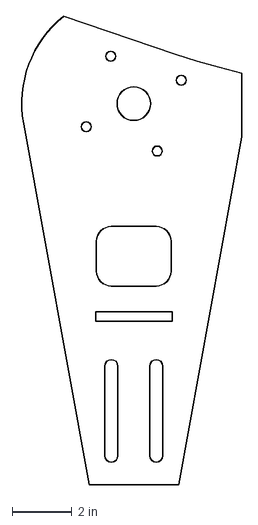
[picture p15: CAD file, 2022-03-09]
dxfs/RightCasterGusset-TotalSketch.dxf
7.55 x 15.7 in

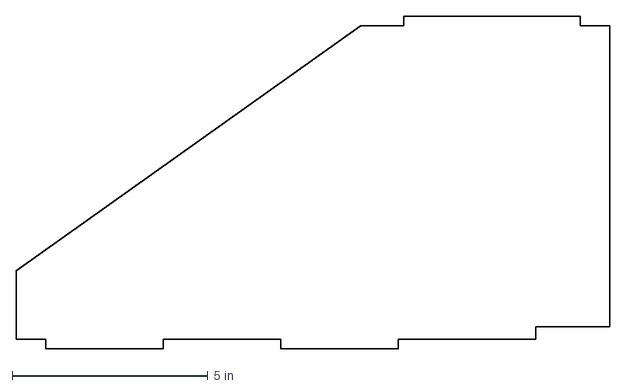
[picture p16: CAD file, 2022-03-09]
dxfs/LeftSidePanel-TotalSketch.dxf
15.1 x 8.50 in

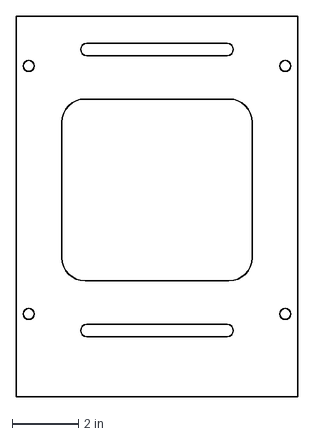
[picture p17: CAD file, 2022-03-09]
dxfs/MotorGusset-TotalSketch.dxf
8.50 x 11.5 in

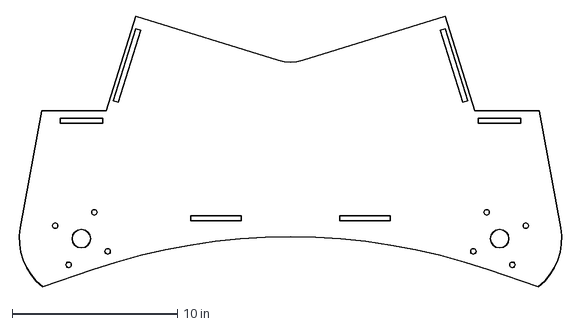
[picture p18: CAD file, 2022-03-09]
dxfs/TopPlate-TotalSketch.dxf
33.2 x 16.4 in

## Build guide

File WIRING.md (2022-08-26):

# Wiring Guide

For the sake of reusability we have wired our VFD into a semi-permanent control panel using DIN terminal blocks to connect the user wiring. **This control panel is designed to be fully enclosed in scenery during use.**

<image alt="Assembled Chassis Before Welding (photo)" src="images/control-panel.jpg" width=400 />

Be sure to follow the VFD manufacturer's specifications when selecing wiring materials. You don't want to under-spec the mains or motor wiring.

## Wiring Guide (For Durapulse GS20)

| Terminal Number | End Point | Name |
| -- | -- | -- |
| **Input Side** |
| G | VFD Ground | Ground |
| `TERMINAL1` | L1 | Input Power Leg 1 |
| `TERMINAL2` | L2 | Input Power Leg 2 |
| `TERMINAL3` | L3 | Input Power Leg 3 |
| **Output Side** |
| G | VFD Ground | Ground |
| `TERMINAL4` | T1 | Motor Turns 1 |
| `TERMINAL5` | T2 | Motor Turns 2 | 
| `TERMINAL6` | T3 | Motor Turns 3 |
| **Safety** |
| `TERMINAL7` | STO +24V | 24V Source For Safety Switches |
| `TERMINAL8` | STO +24V | 24V Source For Safety Switches |
| `TERMINAL9` | STO1 | Safety Input 1 |
| `TERMINAL10` | STO2 | Safety Input 2 |
| **Control** |
| `TERMINAL11` | DCM | Digital Control Common |
| `TERMINAL12` | FWD | Forward Contactor |
| `TERMINAL13` | REV | Reverse Contactor |

## Control Wiring
| Wire | Pin | Terminal | Notes |
| - | - | - | - |
| Emergency Stop Button | 1 | `TERMINAL9` | STO disabled when shorted to +24VDC Source |
| Emergency Stop Button | 4 | `TERMINAL7` | STO +24VDC Source |
| Optional Second Emergency Stop Button | 1 | `TERMINAL10` | STO disabled when shorted to +24VDC Source |
| Optional Second Emergency Stop Button | 4 | `TERMINAL8` | STO +24VDC Source |
| Control Pendant | 1 | `TERMINAL11` | Voltage Sink for Digital Control |
| Control Pendant | 2 | `TERMINAL13` | REVERSE when shorted to votlage sink |
| Control Pendant | 3 | `TERMINAL12` | FORWARD when shorted to votlage sink |

*Note: When not using the optional second emergency stop button you must have a jumper between `TERMINAL8` and `TERMINAL10`.*

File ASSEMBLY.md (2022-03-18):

# Turntable Traction Drive Assembly Guide

I've tried to use off-the-shelf parts as much as possible in order to make this design accessible. The vast majority of the hardware is sourced from McMaster-Carr. This should provide a reliable source for maintenance and customizations. In some cases I've gone to Amazon and Ebay to get parts which are otherwise too expensive.

A Complete Bill Of Materials is available here: [Bill Of Materials](BOM.md)

## Note to Makers

By following these instructions and building this machine you will be creating a powerful piece of machinery which will last a long time. Pause to consider both the longevity of the machine and how that may impact your continuing liability.

:warning: **Before Proceeding, make sure you have read and understood the [SAFETY](SAFETY.md) section of the documentation.**

:warning: **Before Proceeding, make sure you have read and understood the [Limitations](SAFETY.md#Limitations) section of the documentation.**

## Parts Arrival

<image alt="Custom Parts As Delivered" src="images/steel-delivery.jpg" width=400 />

The overall weight of the custom parts for the chassis is approximately 112lbs. Our source delivered the steel parts all bundled together sitting on top of some blocks of wood. No single part it so heavy that it can't be moved by one person, but the bundle was too heavy and bulky for one person to comfortably lift.

<image alt="Parts Test Fit" src="images/parts-fitup.jpg" width=400 />

The very first thing we did is test fit the parts together. I was expecting to have to make some adjustments with an angle grinder, but none were needed. The parts fit perfectly. Fitment was tight enough that the machine held its shape without clamps.

## Welding

Assembly took two days, with the majority of time being spent drilling and tapping holes. The welding of the chassis was a bit time consuming owing to underpowered welder. We used flux-core .030 wire on our 120VAC Hobart Handler 140. 

We first welded the `Motor Gusset` to the base plate using c-clamps for hold-down. The `Motor Gusset` has two long weld slots cut into it in front of and behind the motor bolts. These slots allow for a good strong hold to prevent the gusset from separating from the baseplate.

<image alt="Right Caster Gusset Welded" src="images/right-gusset.jpg" width=400 />

Next the `Caster Gussets` were welded into place. We used the tabs on the `Pusher Plates` to locate the slots before welding. C-clamps were used for hold-down. A generous weld-pocket is provided in the drawing in between the slot for the `Pusher Plate` and the hole for the axle.

<image alt="Initial Welds" src="images/initial-welds.jpg" width=400 />

Next the two `Side Panels`, the `Front Plate`, and the `Pusher Plates` are welded. We set them all in their slots and put the `Top Plate` on top to lock them in place. 90-degree mag-clamps locked everything in place while we put in tack welds. We then then layed about 3" of bead down on either side of each piece. 

In almost all cases we're welding an edge to a non-edge piece of steel. **It's important to manage your heat to avoid blasting away the edges of the steel.** Even on our low-powered welder we had to take care.

:warning: **IMPORTANT! Don't weld the top on until you've tapped the holes!**

## Hardware

In order to mount hardware you must drill then tap the bolt holes. In this design, all bolt holes are undersized for 3/8-24 with the idea being that plasma-cut holes are not very accurate so it's better to drill them after the fact and then tap the perfectly drilled holes. This worked fairly well but we broke plenty of bits and taps.

<image alt="Drilling and Tapping" src="images/drilling-tapping.jpg" width=400 />

We found that the steel fit together perfectly on the day it arrived, but on the second day the top plate no longer fit perfectly on the welded-up sides. It seems like everything moved a little bit as it cooled down from being welded and this caused us some difficulty in assembly. Next time around we will weld the whole machine in a single session. Or perhaps keep the top tacked after the bottom is assembled.

<image alt="Right Drive Wheel" src="images/bottom-chain.jpg" width=300 />

The right-angle (Left/Right AKA Top/Bottom) configuration of the gear-reducer allows us to run one sprocket on top and another sprocket on the bottom. This is useful since 7/8" ID sprockets are quite beefy. Too beefy to fit both chains on a single output shaft from the gear-reducer. For the right-hand drive wheel we connected a ANSI #40 chain to an 11 tooth sprocket mounted on the bottom shaft.

<image alt="Left Drive Wheel" src="images/top-chain.jpg" width=400 />

On the left-hand of the machine we ran chain from a sprocket mounted on the top shaft of the gear-reducer. On this machine the chain is a bit too close to the top plate. In our next revision we'll try to lower the motor 1/4" by eliminating the motor gusset.

<image alt="Painted with handles" src="images/painted-chassis.jpg" width=300 />

During our initial assembly we waited to weld the top until we verified that everything fit correctly. This isn't neccesary since all the hardware can be swapped-out even after the chassis is fully welded. After our test assembly we ran the machine at speed, adjusted it and then removed all the hardware for paint. We painted the chassis using oil-based black satin-finish paint.

<image alt="Painted with handles" src="images/painted-with-handles.jpg" width=300 />

We also welded on some store-bought handles in order to make moving the machine slightly less cumbersome.

## Drive Chain

Connecting the input and output sprockets can be a bit tricky for a few reasons:

- There isn't that much room between the top plate of the machine and where the top chain wants to run. 
- The hub-to-hub distance on the left side of the machine is different on the right side. You may have to experiment by adding links until you find a length of chain that fits evently on both sides.

Move the motor forward and backwards as needed using the motor mount sled. When you find the correct chain length and tension tighten the bolts on the motor flange to lock the motor spacing into the system.

While some chain noise is expected, if your machine is much louder than you expect look for the following defects:

- Chain is too close to the top plate and rubbing against it.
- Sprockets are not at the same height.

If you're still having chain noise try adding grease.

## Motor Wiring

Generally speaking wiring up a 3-phase motor is a matter of consulting the label on the side of the motor and connecting the appropriate wires to the VFD. Typically you will connect 3 hot legs and a ground to the VFD. There is no need for a seperate neutral connection.

<image alt="Motor Wiring" src="images/motor-wiring.jpg" width=300 />

In our General Electric motor the connections look like this:

| VFD Connection | Motor Connection |
| -- | -- |
| Ground | Chassis Ground |
| Leg 1 | Brown and Orange |
| Leg 2 | Blue and Pink | 
| Leg 3 | Tan and Red |
| (No Connection) | Yellow, Black, Purple (Connected together for Wye configuration) |

Be sure to use an appropriate strain relief or grommet to prevent the knockout of the motor's wiring box from abrading the power cable.

## VFD Wiring

For control wiring we have decided used 4-pin XLR. **Industrial automation hardware tends to work with 24VDC reference signals which we intend to use in our control pendant.** For this reason it's important that our choice of cabling no be prone to confusion. 4-pin XLR is unlikely to be accidentally plugged into a dimmer or a soundboard. There is some risk of confusion around theater headsets and around scrollers and TV cameras, but generally it's a lightly-used form factor.

Follow your VFD's instructions for mains wiring. We are using a DURApulse GS23-22P0 in our 3-phase environment. This is a 3phase VFD with a 2HP rating and a STO feature. For reference, we have tested the Turntable Traction Drive on a Hitachi L100 connected to a single 20A 120VAC circuit. So you can definitely use a smaller VFD where required.

### DURApulse GS23 Wiring

**To Begin: Configure the DI pins into `SOURCE` mode my adjusting the toggle switch to `PNP`.**

| XLR Pin Number | VFD Pin | Note |
| -- | -- | -- |
| `XLR Pin 1` | `+24` Digital Common | |
| `XLR Pin 2` | `FWD/DI1` Forward RUN | 3-Wire Configuration |
| `XLR Pin 3` | `REV/DI2` Reverse RUN | 3-Wire Configuration |
| `XLR Pin 4` | `STO1` Safe Torque Off 1 | Interrupting +24V to STO will send e-stop the device. |

| Operation | Condition |
| -- | -- |
| Run Forward | Short `XLR Pin 1` to `XLR Pin 2` |
| Run Reverse | Short `XLR Pin 1` to `XLR Pin 3` |
| Emergency Stop (STO) | Interrupt +24v between `XLR Pin 1` to `XLR Pin 4` |

### Hitachi L100 Wiring

| XLR Pin Number | VFD Pin | Note |
| -- | -- | -- |
| `XLR Pin 1` | `P24` 24VDC Reference | |
| `XLR Pin 2` | `Terminal 1` Forward RUN | Default Configuration |
| `XLR Pin 3` | `Terminal 2` Reverse RUN | Default Configuration |
| `XLR Pin 4` | `Terminal 3` External TRIP | Configure to `EXT` by setting `C_03` to `12` |

In this configuraion you may peform the following operations:

| Operation | Condition |
| -- | -- |
| Run Forward | Short `XLR Pin 1` to `XLR Pin 2` |
| Run Reverse | Short `XLR Pin 1` to `XLR Pin 3` |
| Emergency Stop | Short `XLR Pin 1` to `XLR Pin 4` |

## Control Pendant Wiring

Rather than designing a bespoke pendant I decided to choose from one of the many "Lift Control" pendants available on Amazon. These pendants all seem to feature a rugged enclosure, an e-stop switch and two momentary push buttons. (One added benefit of some crane controls is that they tend to feature mechanical interlocks to prevent the clockwise button and the counter-clockwise button from being pressed at the same time. This isn't strictly necessary but may prevent operator confusion.)

<image alt="Left Drive Wheel" src="images/pendant.jpg" width=300 />

For our implementation we have made the top momentary switch the `RUN FORWARD` button. The bottom momentary switch is the `RUN REVERSE` button:

### Pendant Wiring for DURApulse GS23

| Connection | Purpose |
| -- | -- |
| `XLR Pin 1` TO `EMERGENCY STOP LEFT SIDE` | 24VDC for the pendant will travel through the e-stop button. If e-stop is activated power is interrupted. |
| `XLR Pin 1` TO `RUN FORWARD LEFT SIDE` | Send 24VDC to the `RUN FORWARD` button when e-stop is not engaged. |
| `XLR Pin 1` TO `RUN REVERSE LEFT SIDE` | Send 24VDC to the `RUN REVERSE` button when e-stop is not engaged. |
| `EMERGENCY STOP RIGHT SIDE` TO `XLR Pin 4` | If e-stop is activated interrupt 24VDC to STO1. STO will engage. |
| `RUN FORWARD RIGHT SIDE` TO `XLR Pin 2` | Send 24VDC to the VFD when `RUN FORWARD` is pressed. |
| `RUN REVERSE RIGHT SIDE` TO `XLR Pin 3` | Send 24VDC to the VFD when `RUN REVERSE` is pressed. |

### Pendant Wiring for Hitachi L100

**The Hitachi L100 has no STO device. This configuration does not protect against a malfunctioning VFD.**

| Connection | Purpose |
| -- | -- |
| `XLR Pin 1` TO `EMERGENCY STOP LEFT SIDE` | 24VDC for the pendant will travel through the e-stop button. If e-stop is activated power is interrupted. |
| `EMERGENCY STOP RIGHT SIDE` TO `RUN FORWARD LEFT SIDE` | Send 24VDC to the `RUN FORWARD` button when e-stop is not engaged. |
| `EMERGENCY STOP RIGHT SIDE` TO `RUN REVERSE LEFT SIDE` | Send 24VDC to the `RUN REVERSE` button when e-stop is not engaged. |
| `RUN FORWARD RIGHT SIDE` TO `XLR Pin 2` | Send 24VDC to the VFD when `RUN FORWARD` is pressed and the e-stop is not engaged. |
| `RUN REVERSE RIGHT SIDE` TO `XLR Pin 3` | Send 24VDC to the VFD when `RUN REVERSE` is pressed and the e-stop is not engaged. |

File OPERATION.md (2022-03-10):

# Turntable Traction Drive Operation Guide

This guide is designed to provide procedures for operating the Turntable Traction Drive.

:warning: **Before Proceeding, make sure you have read and understood the [SAFETY](SAFETY.md) section of the documentation.**

:warning: **Before Proceeding, make sure you have read and understood the [Limitations](SAFETY.md#Limitations) section of the documentation.**

## Determining Safe Working Parameters

Once the Turntable Traction Drive has been integrated into your scenery you need to determine safe working values for the various parameters of your VFD.

In particular:
- Operating Frequency
- Acceleration Time
- Deceleration Time
- Current Limit

### Operating Frequency

The operating frequency is the speed at which the drive motor runs. If a motor has a 60Hz native frequency then you should consider 60Hz to be 100% speed.

Determining a safe operating speed involves many factors and there may not be simple way to determine what's safe. 

Observe the following:

- Always set an extremely slow Acceleration/Deceleration time when experimenting with speed.
- Always work your way up from a low speed to a high speed gradually.

Consider the following:

- Consider two people on a turntable may experiene different forces depending on their mass, height distance from the center.
- Consider that stepping on and off a moving turntable is dangerous and should be avoided.
- Consider that technicians working in proximity to a turntable may accidentally come into contact with it during shifts.

### Acceleration/Deceleration

The Acceleration Time and Deceleration Time control how long it takes the drive to come up to full speed and how long it takes to slow down. Anytime that the motor is changing speed there is additional risk to on-stage personel, particularly when acceleration itself changes.

Observe the following:

- Avoid sub-second acceleration/deceleration times.
- Do not change acceleration/deceleration times without rehearsing under the new parameters.

Consider the following:

- Changing accelerations cause a "jerk" sensation. Where possible use linear acceleration parameters.

### Current Limits

If your VFD permits it, consider setting as low a current limit as possible. This will allow your drive and motor to stall if your turntable meets unexpected resistance.

It may be neccesary to tune this parameter so that your VFD has suffient "starting torque" but will still stall if required.

## Operations Checklist

Before each use the Turntable Traction Drive should be inspected to ensure that it is properly installed and safe to use.

| Checkpoint | Ready |
| -- | -- |
| Check machine/turntable pressure on left and right sides. | :black_square_button: |
| Check to make sure drive-wheel is contacting the correct portion of the turntable on left and right sides. | :black_square_button: |
| Check to make output-shaft sprockets have not slipped and are aligned with the power-sprockets. | :black_square_button: |
| Visually inspect turntable circumference and remove any obstructions which may cause jamming. | :black_square_button: |
| Remove parking brake (or disablement device) | :black_square_button: |
| Connect controller to Drive | :black_square_button: |
| Connect drive to power | :black_square_button: |
| Test left and right rotation at performance speed. Listen for any unusual noises coming from the Turntable Traction Drive or the turntable itself.  | :black_square_button: |
| Test left and right rotation at performance speed. Watch for any unusual rubbing, slippage or stalling.  | :black_square_button: |
| Test local emergency stop button. | :black_square_button: |

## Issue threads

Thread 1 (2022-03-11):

Current E-Stop Design Does Not Prevent Runaway VFD

zorlack, 2022-03-11:
Consider using some kind of safety contactor to make-safe the VFD in the case of E-Stop.

From my research utilizing a VFD with **STO** features should resolve this.

zorlack, 2022-03-11:
Consider:

https://www.automationdirect.com/adc/shopping/catalog/drives_-a-_soft_starters/ac_variable_frequency_drives_(vfd)/general_purpose/gs23-23p0

200V 3Phase input
STO
Torque Limiting

zorlack, 2022-03-11:
Alternatively Delta VFD7A5MS23ANSAA

200V 3Phase Input
STO
Torque limiting... crappy docs.

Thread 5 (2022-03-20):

Consider Removable Top

zorlack, 2022-03-20:
We could add holes setup for 1/2" bolts in 2-ply areas of the design. These bolts would allow the user to secure the top plate without welding.

This would aid the serviceability of the machine.

It would require:
- Changes to the top-plate design to facilitate the hold-down
- A modified two-ply baseplate for securing the rear of the top-plate
- 1/2 threaded rod cut to fit.
- Drill bit for 1/2" threads
- Tap for 1/2" threads

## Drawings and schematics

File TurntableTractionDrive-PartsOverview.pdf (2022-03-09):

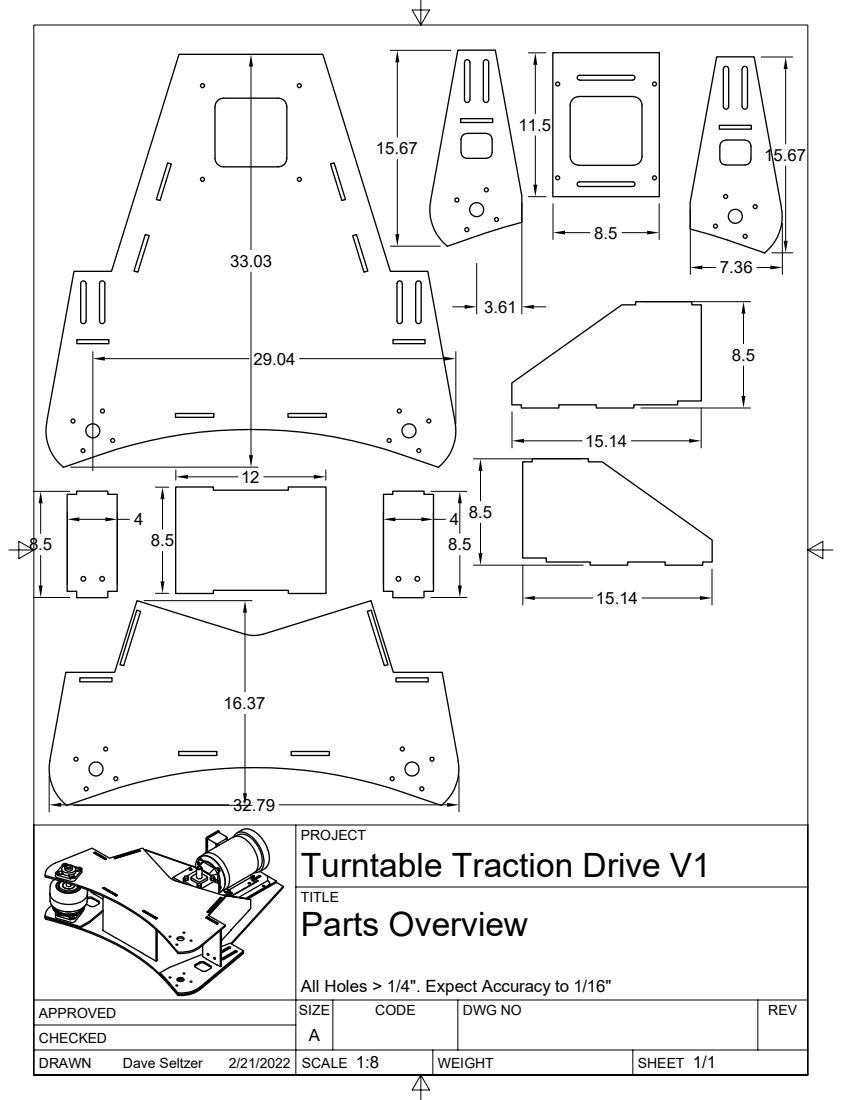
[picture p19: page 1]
PROJECT; TITLE; DRAWN; CHECKED; APPROVED; SCALE; WEIGHT; SHEET; SIZE; CODE; DWG NO; REV; Dave Seltzer

Turntable Traction Drive V1
Parts Overview

All Holes > 1/4". Expect Accuracy to 1/16"

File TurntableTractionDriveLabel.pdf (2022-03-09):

## WARNING TURNTABLE TRACTION DRIVE

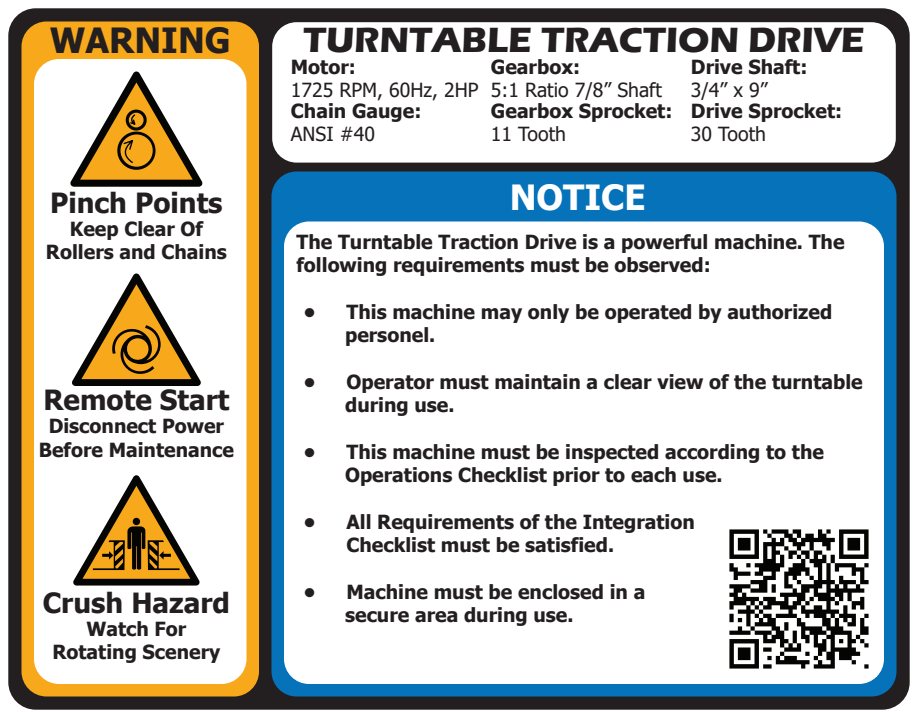
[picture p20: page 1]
NOTICE; Motor: 1725 RPM, 60Hz, 2HP; Gearbox: 5:1 Ratio 7/8” Shaft; Drive Shaft: 3/4” x 9”; Chain Gauge: ANSI #40; Gearbox Sprocket: 11 Tooth; Drive Sprocket: 30 Tooth; Remote Start Disconnect Power Before Maintenance; Crush Hazard Watch For Rotating Scenery

Pinch Points
Keep Clear Of
Rollers and Chains

The Turntable Traction Drive is a powerful machine. The
following requirements must be observed:
• This machine may only be operated by authorized
personel.
• Operator must maintain a clear view of the turntable
during use.
• This machine must be inspected according to the
Operations Checklist prior to each use.
• All Requirements of the Integration
Checklist must be satisfied.
• Machine must be enclosed in a
secure area during use.

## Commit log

2022-03-09 Initial import
    [BottomPlate-TotalSketch.dxf, FrontPlate-TotalSketch.dxf, LeftCasterGusset-TotalSketch.dxf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]
2022-08-26 Update WIRING.md
    Clarify naming of TERMINAL names
